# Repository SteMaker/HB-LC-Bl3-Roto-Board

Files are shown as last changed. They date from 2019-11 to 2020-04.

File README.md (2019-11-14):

# HB-LC-Bl2-24VRain-Board
Selbstbau HomeMatic Hardware mit zwei 24V Rolladenaktoren und einem 230V Rolladenaktor.

## Überblick
**Achtung: Ich übernehme keinerlei Verantwortung für die Sicherheit und Funktionsfähigkeit der Hardware wie auch der Firmware! Die Hardware verwendet Netzspannung 230V ist deshalb lebensgefährlich!**

Firmware: TODO

Ich verwende die Schaltung als Ersatz für eine Rototronic von roto für meine Dachfenster. Der Fensterantrieb und die Verdunklung laufen mit 24V DC Motoren, der Sonnenschutzrollo mit 230V. Der Roto Regensensor kann nicht angeschlossen werden, ich verwende ihn an https://github.com/SteMaker/HB-LC-Bl2-24VRain-Board.

## Dankeschön
Ein dickes, fettes Dankeschön an die homematic community sowas zu ermöglichen, insbesondere an pa-pa, Jérôme und Marco.

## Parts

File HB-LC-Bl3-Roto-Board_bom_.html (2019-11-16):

Source File | /home/stefan/workspace/homematic/HB-LC-Bl3-Roto-Board/HB-LC-Bl3-Roto-Board.sch
BoM Date | Sa 16 Nov 2019 21:51:14 CET
Schematic Version
Schematic Date
PCB Variant | [u'default']
KiCad Version | Eeschema 5.1.4-e60b266~84~ubuntu18.04.1
Component Groups | 24
Component Count (per PCB) | 59
Fitted Components (per PCB) | 59
Number of PCBs | 1
Total Component Count (for 1 PCBs) | 59
 | Description | Part | References | Value | Footprint | Quantity Per PCB | Datasheet | reichelt
1 | Unpolarized capacitor | C | C3 C6 C7 C8 C9 C10 | 100n | C_Rect_L4.6mm_W3.0mm_P2.50mm_MKS02_FKP02 | 6 | ~ | MKS02-63 100N
2 | Unpolarized capacitor | C | C1 C2 | 10µF | CP_Radial_D5.0mm_P2.50mm | 2 | ~ | RAD 10/63
3 | Unpolarized capacitor | C | C4 C5 | 1u | C_Rect_L7.2mm_W5.5mm_P5.00mm_FKS2_FKP2_MKS2_MKP2 | 2 | ~ | MKS2-63 1,0u
4 | 100V 0.15A standard switching diode, DO-35 | 1N4148 | D1 D2 D3 D4 D5 D6 | 1N4148 | D_DO-35_SOD27_P2.54mm_Vertical_AnodeUp | 6 | http://www.nxp.com/documents/data_sheet/1N4148_1N4448.pdf | 1N 4148
5 | Fuse | Fuse | F1 | Fuse | Fuseholder_Cylinder-5x20mm_Schurter_FPG4_Vertical_Closed | 1 | ~ | PL FPG4-40
6 |  | ArduinoProMini | IC1 | ArduinoProMini | pro_mini | 1 | http://www.arduino.cc/en/uploads/Main/Arduino-Pro-Mini-schematic.pdf
7 |  | 236-402 | J4 | 230V | TerminalBlock_WAGO_236-102_1x02_P5.00mm_45Degree | 1 | ~ | WAGO 236-402
8 |  | 250-x02 | J5 | 24V | P-250-402 | 1 | ~ | WAGO 250-402
9 |  | 250-x02 | J6 | Motor Fenster 24V | P-250-402 | 1 | ~ | WAGO 250-402
10 |  | 236-403 | J7 | Motor Sonnenschutz 230V | TerminalBlock_WAGO_236-103_1x03_P5.00mm_45Degree | 1 | ~ | WAGO 236-403
11 |  | 250-x02 | J8 | Motor Verdunklung 24V | P-250-402 | 1 | ~ | WAGO 250-402
12 |  | 250-x03 | J2 | Taster Fenster | P-250-403 | 1 | ~ | WAGO 250-403
13 |  | 250-x03 | J3 | Taster Sonnenschutz | P-250-403 | 1 | ~ | WAGO 250-403
14 |  | 250-x03 | J1 | Taster Verdunklung | P-250-403 | 1 | ~ | WAGO 250-403
15 | Compact, Industry-Standard 2-pole relay, designed to switch 2A Signal Loads, Single-side Stable | G6S-2 | K1 K2 K3 K4 | G6S-2 | Relay_DPDT_Omron_G6S-2 | 4 | http://omronfs.omron.com/en_US/ecb/products/pdf/en-g6s.pdf | G6S-2 24DC
16 | 0.8A Ic, 45V Vce, NPN Transistor, TO-92 | BC337 | Q1 Q2 Q3 Q4 Q5 Q6 | BC337 | TO-92L_Wide | 6 | http://www.nxp.com/documents/data_sheet/BC817_BC817W_BC337.pdf | RND BC337
17 | Resistor | R | R7 R8 R11 R12 R15 R17 | 10k | R_Axial_DIN0204_L3.6mm_D1.6mm_P5.08mm_Horizontal | 6 | ~ | 1/4W 10k
18 | Resistor | R | R4 R5 | 2k4 | R_Axial_DIN0204_L3.6mm_D1.6mm_P2.54mm_Vertical | 2 | ~ | 1/4W 2,4k
19 | Resistor | R | R9 R10 R13 R14 R16 R18 | 47 | R_Axial_DIN0204_L3.6mm_D1.6mm_P5.08mm_Horizontal | 6 | ~ | 1/4W 47
20 | Resistor | R | R1 R2 R3 R6 | 7k5 | R_Axial_DIN0204_L3.6mm_D1.6mm_P2.54mm_Vertical | 4 | ~ | 1/4W 7,5K
21 |  | FINDER-40.61 | RL2 RL4 | FINDER-40.61 | FIN4061 | 2 |  | FIN 40.61.9 24V
22 | Push button switch, generic, two pins | SW_Push | SW1 | SW_Push | SW_PUSH_6mm_H4.3mm | 1 | ~ | TASTER 3301
23 |  | AM1S-xxxxS | U1 | AM1S-xxxxS | SIL-4 | 1 |  | SIM1-2403 SIL4
24 |  | CC1101 | U3 | CC1101-868MHz-Module | CC1101_Module | 1 | http://www.digirf.com/XWFU/2013/4f3751b81deca976.pdf

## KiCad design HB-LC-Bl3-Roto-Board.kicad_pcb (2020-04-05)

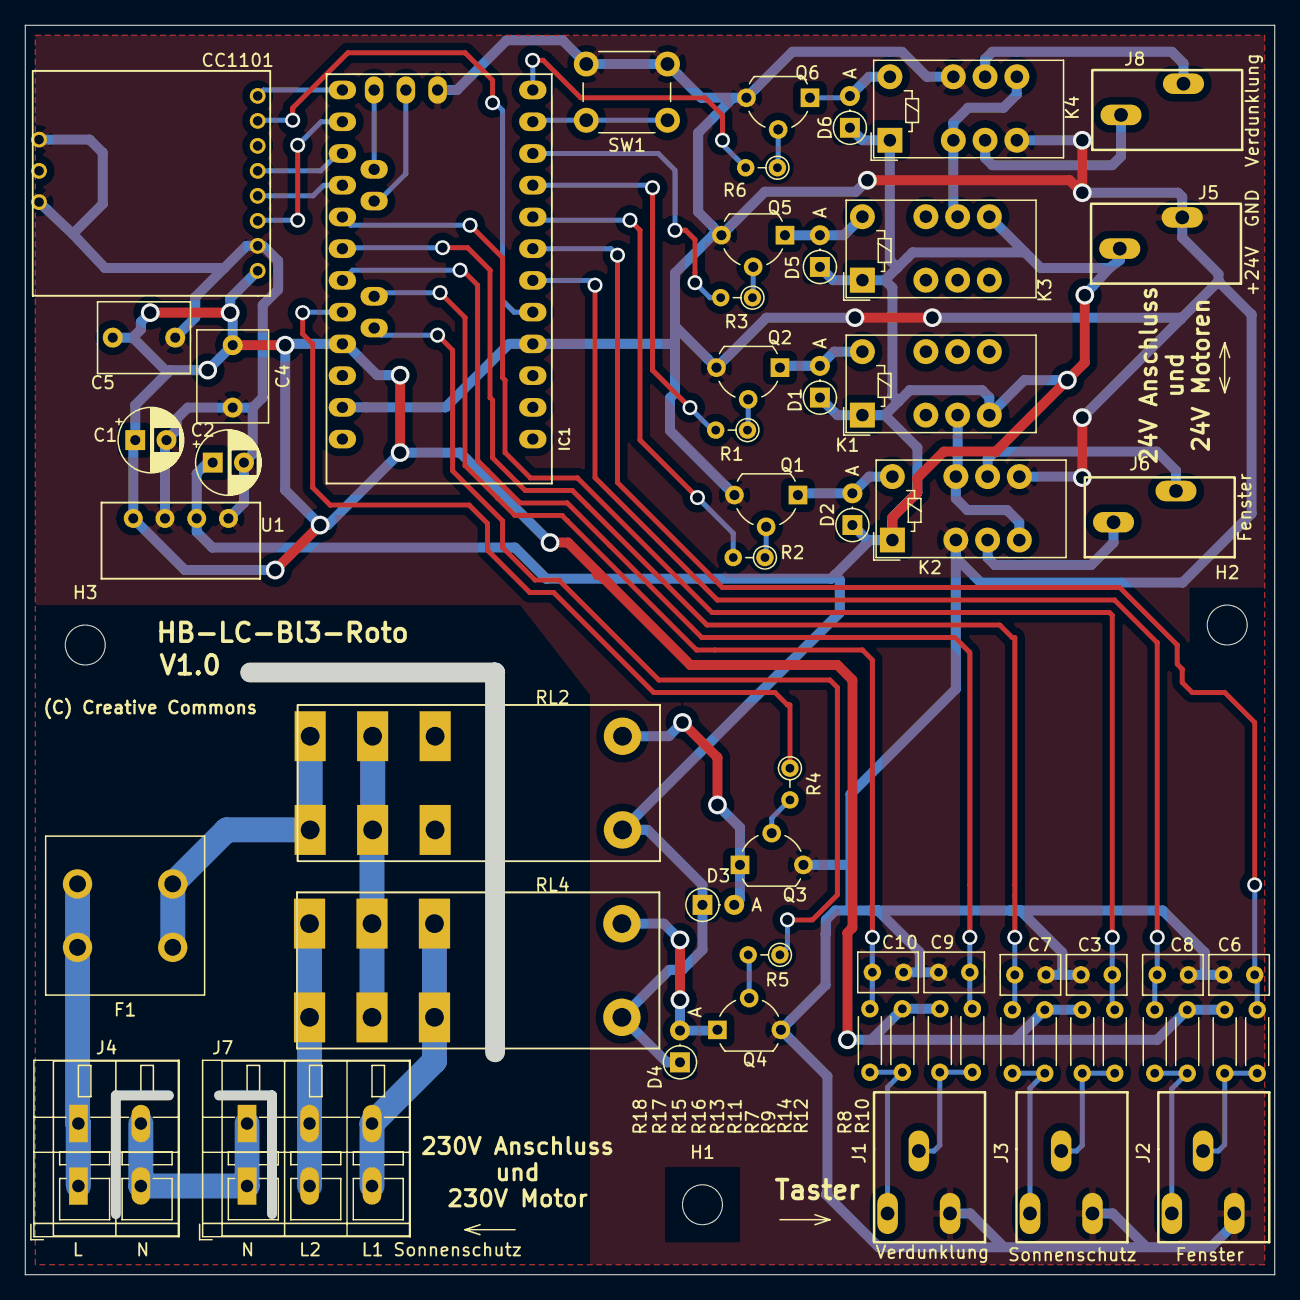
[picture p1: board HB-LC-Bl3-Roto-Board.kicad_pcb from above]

Board: 2 copper layers, 100.0 x 100.0 mm, 62 parts (0 on the bottom side), 52 nets.

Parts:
C1, C2: 10µF; CP_Radial_D5.0mm_P2.50mm
C3, C6, C7, C8, C9, C10: 100n; C_Rect_L4.6mm_W3.0mm_P2.50mm_MKS02_FKP02
C4, C5: 1u; C_Rect_L7.2mm_W5.5mm_P5.00mm_FKS2_FKP2_MKS2_MKP2
D1, D2, D3, D4, D5, D6: 1N4148; D_DO-35_SOD27_P2.54mm_Vertical_AnodeUp
F1: Fuse; Fuseholder_Cylinder-5x20mm_Schurter_FPG4_Vertical_Closed
H1, H2, H3: MountingHole; MountingHole_3.2mm_M3
IC1: ArduinoProMini; pro_mini
J1: Taster Verdunklung; P-250-403
J2: Taster Fenster; P-250-403
J3: Taster Sonnenschutz; P-250-403
J4: 230V; TerminalBlock_WAGO_236-102_1x02_P5.00mm_45Degree
J5: 24V; P-250-402
J6: Motor Fenster 24V; P-250-402
J7: Motor Sonnenschutz 230V; TerminalBlock_WAGO_236-103_1x03_P5.00mm_45Degree
J8: Motor Verdunklung 24V; P-250-402
K1, K2, K3, K4: G6S-2; Relay_DPDT_Omron_G6S-2
Q1, Q2, Q3, Q4, Q5, Q6: BC337; TO-92L_Wide
R1, R2, R3, R6: 7k5; R_Axial_DIN0204_L3.6mm_D1.6mm_P2.54mm_Vertical
R4, R5: 2k4; R_Axial_DIN0204_L3.6mm_D1.6mm_P2.54mm_Vertical
R7, R8, R11, R12, R15, R17: 10k; R_Axial_DIN0204_L3.6mm_D1.6mm_P5.08mm_Horizontal
R9, R10, R13, R14, R16, R18: 47; R_Axial_DIN0204_L3.6mm_D1.6mm_P5.08mm_Horizontal
RL2, RL4: FINDER-40.61; FIN4061
SW1: SW_Push; SW_PUSH_6mm_H4.3mm
U1: AM1S-xxxxS; SIL-4
U3: CC1101-868MHz-Module; CC1101_Module

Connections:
+3V3: C1.1, C4.1, C5.2, IC1.21, R7.1, R8.1, R11.1, R12.1, R15.1, R17.1, U1.4, U3.1
+24V: C2.1, D1.1, D2.1, D3.1, D4.1, D5.1, D6.1, J5.L2, K1.1, K1.5, K2.1, K3.1, K3.8, K4.1, RL2.A1, RL4.A1, U1.2
/L: F1.2, J4.1
/L_FUSED: F1.1, RL2.14, RL2.24
/M1_A: J6.L1, K2.9
/M1_B: J6.L2, K2.4
/M1_DIR: IC1.8, R2.2
/M1_EN: IC1.9, R1.2
/M2_DIR: IC1.26, R5.1
/M2_EN: IC1.20, R4.1
/M2_L: RL2.11, RL2.21, RL4.11, RL4.21
/M2_L1: J7.3, RL4.12, RL4.22
/M2_L2: J7.2, RL4.14, RL4.24
/M3_A: J8.L2, K4.4
/M3_B: J8.L1, K4.9
/M3_DIR: IC1.12, R6.2
/M3_EN: IC1.10, R3.2
/N: J4.2, J7.1
/RF_CSN: IC1.13, U3.8
/RF_INT: IC1.5, U3.7
/RF_MISO: IC1.15, U3.5
/RF_MOSI: IC1.14, U3.3
/RF_SCLK: IC1.16, U3.4
/TA1: C6.1, IC1.7, R10.1
/TA1_IN: J2.L2, R8.2, R10.2
/TA2: C8.1, IC1.6, R14.1
/TA2_IN: J2.L1, R12.2, R14.2
/TA3: C3.1, IC1.17, R9.1
/TA3_IN: J3.L2, R7.2, R9.2
/TA4: C7.1, IC1.18, R13.1
/TA4_IN: J3.L1, R11.2, R13.2
/TA5: C9.1, IC1.19, R16.1
/TA5_IN: J1.L2, R15.2, R16.2
/TA6: C10.1, IC1.25, R18.1
/TA6_IN: J1.L1, R17.2, R18.2
GND: C1.2, C2.2, C3.2, C4.2, C5.1, C6.2, C7.2, C8.2, C9.2, C10.2, IC1.4, IC1.23, IC1.29, J1.L3, J2.L3, J3.L3, J5.L1, K2.3, K2.8, K4.5, K4.10, Q1.3, Q2.3, Q3.3, Q4.3, Q5.3, Q6.3, SW1.2, U1.1, U1.3, U3.2, U3.10, U3.11
unnamed: D1.2, K1.12, Q2.1
unnamed: D2.2, K2.12, Q1.1
unnamed: D3.2, Q3.1, RL2.A2
unnamed: D4.2, Q4.1, RL4.A2
unnamed: D5.2, K3.12, Q5.1
unnamed: D6.2, K4.12, Q6.1
unnamed: IC1.11, SW1.1
unnamed: K1.4, K2.5, K2.10
unnamed: K3.9, K4.3, K4.8
unnamed: Q1.2, R2.1
unnamed: Q2.2, R1.1
unnamed: Q3.2, R4.2
unnamed: Q4.2, R5.2
unnamed: Q5.2, R3.1
unnamed: Q6.2, R6.1
unnamed: RL2.12, RL2.22

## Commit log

2019-11-09 First version of the schematic
    [HB-LC-Bl3-Roto-Board.kicad_pcb, HB-LC-Bl3-Roto-Board.sch]
2019-11-14 Intermediate commit
    [HB-LC-Bl3-Roto-Board.kicad_pcb, HB-LC-Bl3-Roto-Board.sch]
2019-11-16 Version 1
    [HB-LC-Bl3-Roto-Board.kicad_pcb, HB-LC-Bl3-Roto-Board.sch]
2020-02-12 Fixed rotated connector, improved pcb print
    - J6, J5 and J8 are 180° rotated. Still ok to assemble. But some prints
    are no longer readable. Fixed
    - Print of resistor array for R7..R18 is partly wrong. Corrected. Only a
    PCB print issue
    [HB-LC-Bl3-Roto-Board.kicad_pcb, HB-LC-Bl3-Roto-Board.sch]
2020-04-05 Added missing GND connections for CC1101
    [HB-LC-Bl3-Roto-Board.kicad_pcb]
2020-04-05 Updated CC101 footprint
    [HB-LC-Bl3-Roto-Board.kicad_pcb]

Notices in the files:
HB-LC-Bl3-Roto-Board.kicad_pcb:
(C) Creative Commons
